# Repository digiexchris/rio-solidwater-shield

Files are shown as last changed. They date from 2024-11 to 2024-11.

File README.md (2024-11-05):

# rio-SolidWater-Sheild
6 Axis LinuxCNC-RIO Raspberry-PI FPGA-Hat based heavily on rio-IceShield, designed for stepper motors.
**experimental**

Nearly a 100% pin compatible rework of the rio-iceshield using single sided SMD, so that it can be inexpensively manufactured by JLCPCB or other parts fab houses. Some parts have been changed to parts that are available through the fab house, so that all SMD components can be assembled at the fab house.

Maximum step rate is theoretically 500khz due to the minimum rise and fall time of the  though this has not been tested much more than 

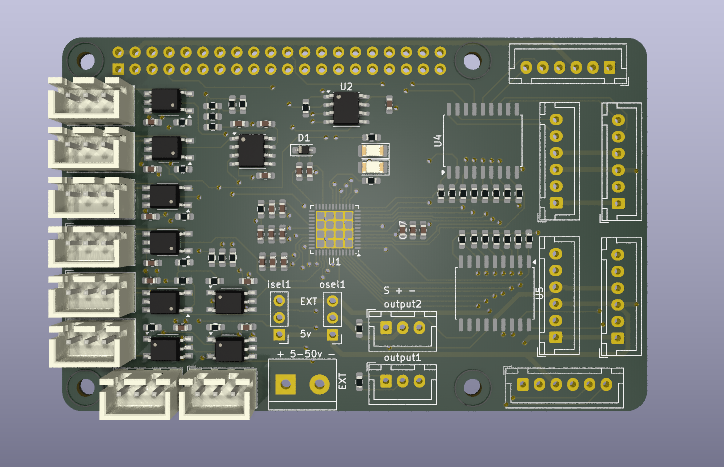
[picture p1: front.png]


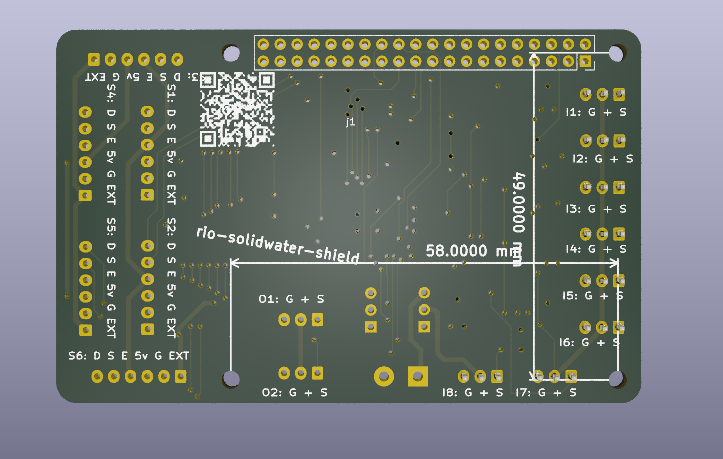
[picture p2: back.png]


## Hardware

- Tested on a Raspberry Pi 4b with the Touchy and Axis UIs. Axis is a bit slow for a pi4 though, I recommend only using it for initial calibration and trying Touchy or another UI.
- If you don't use it on a Pi 4b, you will have to provide a 5mhz clock signal on the pi GPIO header pin 7.
- The 24v power jack is ONLY for input, output, and stepper connections, it will not power the board or pi. You can supply any voltage you wish on there, up to a maximum of 50v, which is the limit of the ULN2803A line driver.
- You can select if the inputs and outputs (not including stepper outputs) supply 5v from the pi or external power from the jack labelled 24v through the isel1 jumper. Short the middle pin to either the top or bottom pin, labelled on the top side of the board. Both 5v and external power is available on all stepper headers. 
- The connectors used are JST-XH 2.54mm pitch. Any 2.54mm or 0.1" pitch connector or pin header will work.

## software / gateware
Requires:
https://github.com/multigcs/riocore

## Ordering:

Production output files are provided in the Production-Outputs directory. JLCPCB required a few small replacements due limits in stock, so the parts that were selected during the assembly step are included in bom.xls, and bom.xls should be able to be uploaded to JLCPCB directly during the assembly ordering step. Select ONLY the top side for assembly, and Economy assembly is fine. The positions.csv is included as well.

Don't be alarmed if during the parts placement confirmation step the parts appear rotated, the fab house will place them in their correct orientation. It's recommended to select "Confirm Parts Placement" so they can send you the generated final placement once they've analyzed it. The parts that I either could not see or needed to fix in the ordering preview ended up corrected when they emailed me the production file before production started.

The gerber files are in the zip file in the same directory. It is a 4 layer board.

There is a minimum pcb order of 5 and a minimum assembly order of 2, and production and assembly cost for me was approximately $50 CAD for 2 boards in 2024. You end up with 3 spare unpopulated boards to use as coasters!

## Usage:

- Setup a https://github.com/multigcs/riocore as normal according to the instructions there.
- Copy the riocore/config/IceShield/config.json
- Generate and compile the config.
- Navigate to the Output dir, and run sudo ./spiflash.sh ./rio.bin
If successful, you probably will see a solid green light on the board.
If not, you may need to add yourself to appropriate SPI groups, or enable SPI on the raspberry pi you're using. Post an issue here if you have trouble with this, I likely have details available on my reference hardware.
This requires a clock signal from the raspberry pi on GPIO header pin 7. There are a few ways to do this, but I did it by installing the WiringPi tooling https://github.com/WiringPi/WiringPi and then executing
```
gpio mode 7 clock
gpio clock 7 5000000
```
You may add this to your Output/IceShield/LinuxCNC/start.sh to automate this.
If that was successful, the green LED should start blinking, assuming your config has the default "blink" plugin setup.

Proceed to setup LinuxCNC as normal according to https://github.com/multigcs/riocore

## Forum
English: https://forum.linuxcnc.org/18-computer/49142-linuxcnc-rio-realtimeio-for-linuxcnc-based-on-fpga-ice40-ecp5

## Derived From
https://github.com/multigcs/rio-iceshield

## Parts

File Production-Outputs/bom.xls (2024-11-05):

Comment | Designator | Footprint | JLCPCB Part #
ELM453-TA-V | U15,U16,U17,U18,U19,U20,U21,U6 | MFSOP6-5_4.4x3.6mm_P1.27mm | C110223
10n | C13,C17,C2 | 0603 | C57112
AT25SF041B-SHD4Mb | U2 | SOIC-8_3.9x4.9mm_P1.27mm | C5127618
LM317LD13TR | U7 | SOIC-8_3.9x4.9mm_P1.27mm | C81457
LED | D2,D3 | 1206 | C965825
1k2 | R33,R34,R35,R36,R37 | 0603 | C22765
1N4148WS | D1 | D_SOD-323_HandSoldering | C2128
100 | R1 | 0603 | C22775
100n | C10,C14,C16,C18,C19,C20,C21,C22,C23,C24,C25,C4,C5,C6,C7,C8,C9 | 0603 | C14663
20k | R13,R14,R15,R16,R17,R18,R19,R20,R21,R22,R23,R24,R25,R26,R27,R28,R29,R30 | 0603 | C4184
1u | C12,C15 | 0603 | C15849
3K3 | R2,R3,R31,R32,R4,R5,R6,R7,R8,R9 | 0603 | C22978
10k | R12 | 0603 | C25804
ULN2803A | U4,U5 | SOP-18_7.495x11.515mm_P1.27mm | C845537
4u7 | C1,C3 | 0603 | C19666
1k | R10,R11 | 0603 | C21190
ICE40UP5K-SG48ITR | U1 | QFN-48-1EP_7x7mm_P0.5mm_EP5.6x5.6mm | C2678152
10u | C11 | 0603 | C19702

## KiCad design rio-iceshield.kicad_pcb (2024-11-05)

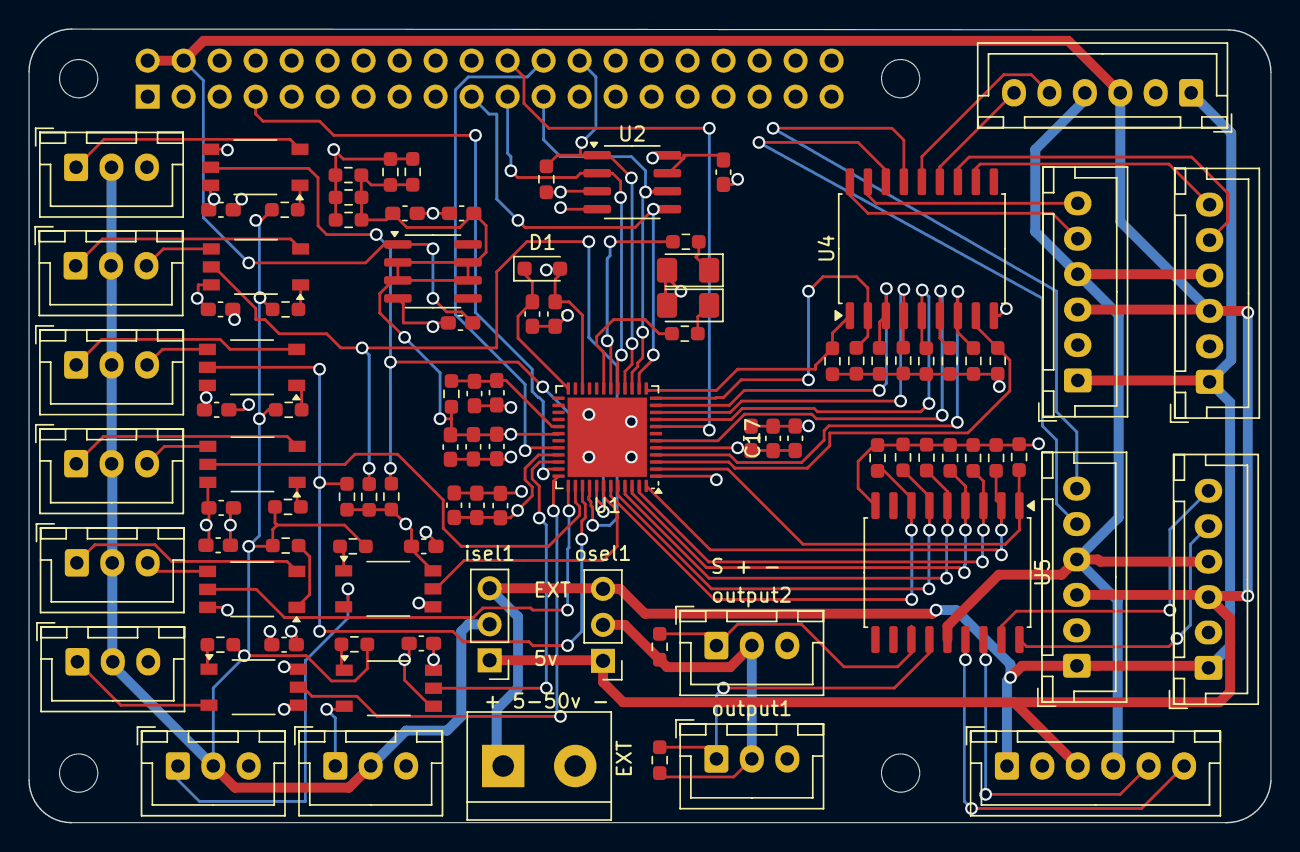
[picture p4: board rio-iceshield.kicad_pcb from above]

Board: 4 copper layers, 87.6 x 56.0 mm, 102 parts (1 on the bottom side), 74 nets.

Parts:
C1, C3: 4u7; C_0603_1608Metric_Pad1.08x0.95mm_HandSolder
C2, C13, C17: 10n; C_0603_1608Metric_Pad1.08x0.95mm_HandSolder
C4, C5, C6, C7, C8, C9, C10, C14, C16, C18, C19, C20, C21, C22, C23, C24, C25: 100n; C_0603_1608Metric_Pad1.08x0.95mm_HandSolder
C11: 10u; C_0603_1608Metric_Pad1.08x0.95mm_HandSolder
C12, C15: 1u; C_0603_1608Metric_Pad1.08x0.95mm_HandSolder
D1: 1N4148WS; D_SOD-323_HandSoldering
D2, D3: LED; LED_1206_3216Metric_Pad1.42x1.75mm_HandSolder
EXT: Screw_Terminal_01x02; TerminalBlock_bornier-2_P5.08mm
J2, J3, J4, J5, J6: Conn_01x06; JST_XH_B6B-XH-A_1x06_P2.50mm_Vertical
Jo1: Conn_01x06; JST_XH_B6B-XH-A_1x06_P2.50mm_Vertical
MH1, MH2, MH3, MH4: MountingHole_2.7mm_M2.5
R1: 100; R_0603_1608Metric_Pad0.98x0.95mm_HandSolder
R2, R3, R4, R5, R6, R7, R8, R9: 3K3; R_0603_1608Metric_Pad0.98x0.95mm_HandSolder
R10, R11: 1k; R_0603_1608Metric_Pad0.98x0.95mm_HandSolder
R12: 10k; R_0603_1608Metric_Pad0.98x0.95mm_HandSolder
R13, R14, R15, R16, R17, R18, R19, R20, R21, R22, R23, R24, R25, R26, R27: 20k; R_0603_1608Metric_Pad0.98x0.95mm_HandSolder
R28, R29, R30: 20K; R_0603_1608Metric_Pad0.98x0.95mm_HandSolder
R31, R32: 3k3; R_0603_1608Metric_Pad0.98x0.95mm_HandSolder
R33, R34, R35, R36, R37: 1k2; R_0603_1608Metric_Pad0.98x0.95mm_HandSolder
U1: ICE40UP5K-SG48ITR; QFN-48-1EP_7x7mm_P0.5mm_EP5.6x5.6mm
U2: AT25SF041B-SHD 4 Mb; SOIC-8_3.9x4.9mm_P1.27mm
U4, U5: ULN2803A; SOP-18_7.495x11.515mm_P1.27mm
U6, U15, U16, U17, U18, U19, U20, U21: ELM453-TA-V; MFSOP6-5_4.4x3.6mm_P1.27mm
U7: LM317LD13TR; SOIC-8_3.9x4.9mm_P1.27mm
input1, input2, input3, input4, input5, input6, input7, input8: Conn_01x03; JST_XH_B3B-XH-A_1x03_P2.50mm_Vertical
isel1: Conn_01x03; PinHeader_1x03_P2.54mm_Vertical
j1: GPIO; PinSocket_2x20_P2.54mm_Vertical
osel1: Conn_01x03; PinHeader_1x03_P2.54mm_Vertical
output1, output2: Conn_01x03; JST_XH_B3B-XH-A_1x03_P2.50mm_Vertical

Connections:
1v2: C2.1, C3.1, C12.1, C13.1, C14.1, C15.1, C16.1, C17.1, R1.1, R33.2, R34.2, R35.2, R36.2, R37.2, U1.5 (VCC), U1.30 (VCC), U7.2 (VO), U7.3 (VO), U7.6 (VO), U7.7 (VO)
2: R21.2, U1.2 (IOB_6a), U5.1 (I1)
2v5: C10.1, D1.1 (K), U1.24 (VPP_2V5)
3: R20.2, U1.3 (IOB_9b), U4.8 (I8)
3v3: C4.2, C5.2, C6.2, C7.2, C9.1, C18.1, C19.1, C20.1, C21.1, C22.1, C23.1, C24.1, C25.1, D1.2 (A), D2.2 (A), D3.2 (A), R12.1, R28.1, R29.1, R30.1, U1.1 (VCCIO_2), U1.22 (SPI_VCCIO1), U1.33 (VCCIO_0), U2.3 (~WP/IO2), U2.7 (~HOLD/IO3), U2.8 (VCC), U6.6, U15.6, U16.6, U17.6, U18.6, U19.6, U20.6, U21.6, j1.1, j1.17
4: R19.2, U1.4 (IOB_8a), U4.7 (I7)
5v: C1.1, J2.3, J3.3, J4.3, J5.3, J6.3, Jo1.3, U7.1 (VI), isel1.1, j1.2, j1.4, osel1.1
6: R18.2, U1.6 (IOB_13b), U4.6 (I6)
9: R17.2, U1.9 (IOB_16a), U4.5 (I5)
10: R16.2, U1.10 (IOB_18a), U4.4 (I4)
11: R15.2, U1.11 (IOB_20a), U4.3 (I3)
12: R14.2, U1.12 (IOB_22a), U4.2 (I2)
12v: EXT.1, J2.1, J3.1, J4.1, J5.1, J6.1, Jo1.1, isel1.3, osel1.3
13: R13.2, U1.13 (IOB_24a), U4.1 (I1)
18: R11.1, U1.18 (IOB_31b)
19: R10.1, U1.19 (IOB_29b)
32: U1.32 (IOT_43a), j1.24
34: U1.34 (IOT_44b), U21.5
35: U1.35 (IOT_46b_G0), j1.7
36: U1.36 (IOT_48b), U19.5
37: U1.37 (IOT_45a_G1), U18.5
38: U1.38 (IOT_50b), U17.5
39: R28.2, U1.39 (RGB0), U16.5
40: R29.2, U1.40 (RGB1), U15.5
41: R30.2, U1.41 (RGB2), U6.5
42: U1.42 (IOT_51a), U20.5
43: R27.2, U1.43 (IOT_49a), U5.7 (I7)
44: R26.2, U1.44 (IOB_3b_G6), U5.6 (I6)
45: R25.2, U1.45 (IOB_5b), U5.5 (I5)
46: R24.2, U1.46 (IOB_0a), U5.4 (I4)
47: R23.2, U1.47 (IOB_2a), U5.3 (I3)
48: R22.2, U1.48 (IOB_4a), U5.2 (I2)
CRESET: U1.8 (~CRESET), j1.22
unnamed: D2.1 (K), R11.2
unnamed: D3.1 (K), R10.2
unnamed: R2.1, U6.1
unnamed: R3.1, U15.1
unnamed: R4.1, U16.1
unnamed: R5.1, U17.1
unnamed: R6.1, U18.1
unnamed: R7.1, U19.1
unnamed: R8.1, U20.1
unnamed: R9.1, U21.1
unnamed: C8.1, C11.1, R1.2, U1.29 (VCCPLL)
unnamed: U6.3, input1.1
unnamed: U15.3, input2.1
unnamed: U16.3, input3.1
unnamed: U17.3, input4.1
unnamed: U18.3, input5.1
unnamed: U19.3, input6.1
unnamed: U20.3, input7.1
unnamed: U21.3, input8.1
SPI_CS1: R12.2, U1.16 (IOB_35b_SPI_SS), U2.1 (~CS), j1.26
SPI_MISO: U1.17 (IOB_33b_SPI_SI), U2.2 (SO/IO1), j1.21
SPI_MOSI: U1.14 (IOB_32a_SPI_SO), U2.5 (SI/IO0), j1.19
SPI_SCK: U1.15 (IOB_34a_SPI_SCK), U2.6 (SCK), j1.23
enable: J2.4, J3.4, J4.4, J5.4, J6.4, Jo1.4, U5.14 (O5)
gnd: C1.2, C2.2, C3.2, C4.1, C5.1, C6.1, C7.1, C8.2, C9.2, C10.2, C11.2, C12.2, C13.2, C14.2, C15.2, C16.2, C17.2, C18.2, C19.2, C20.2, C21.2, C22.2, C23.2, C24.2, C25.2, EXT.2, J2.2, J3.2, J4.2, J5.2, J6.2, Jo1.2, R13.1, R14.1, R15.1, R16.1, R17.1, R18.1, R19.1, R20.1, R21.1, R22.1, R23.1, R24.1, R25.1, R26.1, R27.1, R33.1, R34.1, R35.1, R36.1, R37.1, U1.49 (GND), U2.4 (GND), U4.9 (GND), U5.9 (GND), U6.4, U7.4 (ADJ), U15.4, U16.4, U17.4, U18.4, U19.4, U20.4, U21.4, input1.3, input2.3, input3.3, input4.3, input5.3, input6.3, input7.3, input8.3, j1.6, j1.9, j1.14, j1.20, j1.25, j1.30, j1.34, j1.39, output1.3, output2.3
in_power: R2.2, R3.2, R4.2, R5.2, R6.2, R7.2, R8.2, R9.2, input1.2, input2.2, input3.2, input4.2, input5.2, input6.2, input7.2, input8.2, isel1.2
j1_dir: Jo1.6, U4.17 (O2)
j1_step: Jo1.5, U4.18 (O1)
j2_dir: J2.6, U4.15 (O4)
j2_step: J2.5, U4.16 (O3)
j3_dir: J3.6, U4.13 (O6)
j3_step: J3.5, U4.14 (O5)
j4_dir: J4.6, U4.11 (O8)
j4_step: J4.5, U4.12 (O7)
j5_dir: J5.6, U5.17 (O2)
j5_step: J5.5, U5.18 (O1)
j6_dir: J6.6, U5.15 (O4)
j6_step: J6.5, U5.16 (O3)
out1: R31.1, U5.13 (O6), output1.1
out2: R32.1, U5.12 (O7), output2.1
out_power: R31.2, R32.2, osel1.2, output1.2, output2.2

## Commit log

2024-10-24 Fix missing clk line
    [input.kicad_sch, rio-iceshield.kicad_pcb, rio-iceshield.kicad_sch]
2024-11-05 Documentation update
    [bom.xls, positions.csv, rio-iceshield.kicad_pcb]
